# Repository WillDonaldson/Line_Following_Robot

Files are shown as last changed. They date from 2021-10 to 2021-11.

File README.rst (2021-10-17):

Line Following Robot
====================

An open source beginner-friendly tutorial on building a line following robot with Arduino. 

Tutorial
--------
Hardware build instructions and software documentation here:

https://line-following-robot.willdonaldson.io/

Purchase
--------

This project is open source and a bill of materials is freely provided in the tutorial link (above). However, if you prefer to purchase a prepared robot kit that will also financially support the development of more open source projects then you can purchase the robot here:

<insert link>

License
-------
This project is licensed under the terms of the MIT license

Media
-----

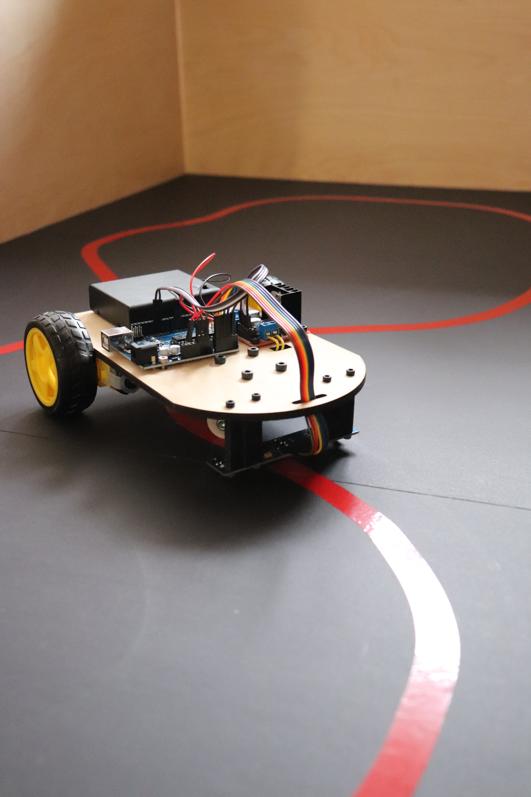
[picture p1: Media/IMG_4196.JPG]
Portrait of line following robot


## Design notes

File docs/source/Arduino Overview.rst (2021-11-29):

Arduino Overview
================

.. note::

   This project is under active development. More updates coming soon.

When documentation is complete this page will serve as a beginner friendly intro into programming with Arduino. In the meantime please refer to the `official Arduino resources <https://www.arduino.cc/reference/en/>`__.

Physical Board
--------------

Programming
-----------

Blink
-----

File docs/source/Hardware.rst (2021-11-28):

Hardware
========

This project is open source and a bill of materials is freely provided (below). However, if you prefer to purchase a prepared robot kit that will also financially support the development of more open source projects then you can purchase the robot here: <coming soon - insert link>

Bill of Materials
-----------------

**Off the shelf components**

* 1x Arduino Uno (with cable)
* 1x L298N Motor Driver
* 1x AA battery holder with ON/OFF switch (4 slots) 
* 4x AA batteries
* 2x Set of TT DC motor gearbox, wheel, mounting bracket, two M3 10mm bolts, two M3 30mm bolts, and two M3 nuts (usually sold all together)
* 1x One inch caster wheel
* 1x Five channel TCRT5000L array 
* 13x Male-Female jumper cables
* 2x Male-Male jumper cables
* 15x M3 12mm bolts
* 4x M4 20mm bolts
* 7x M3 nuts (optional use lock-nuts or loctite)
* 4x M4 nutes (optional use lock-nuts or loctite))
* Extra wire for motor leads (18 AWG - 22AWG)
* Zipties (optional for cable management)
* Double sided tape or hot glue for securing the battery pack

**Components to be fabricated**
See the next section for more details

* 1x Robot body (laser cut from 3mm to 5mm wood or acrylic)
* 1x Caster wheel spacer (3D printed)
* 2x Infrared sensor standoffs (3D printed)

**Tools**

* Soldering iron and solder
* Computer and approatiate dongle/cable for connecting to Arduino Uno
* Wire strippers (optional)
* Multimeter (optional - for diagnostics)

Manufacturing
-------------

When it comes to robotics, being able to fabricate custom components is extremely valuable, however buying your own 3D printer, laser cutter, and/or CNC machine is cost probihitive to starting a journey into robotics. Fortunately these custom pieces are available for purchase from my website <insert link - coming soon>. Alternatively online 3D printing services are available, and for some, these tools may be available locally at makerspaces, public libraries, or universities at little or no cost. These components are not dimension critical so they can also be fabricated by hand out of scrap wood and a hand drill or even out of sheets of cardboard.

**Robot body**

The SVG file for laser cutting the body can be downloaded `here <https://github.com/WillDonaldson/Line_Following_Robot/blob/main/Fabrication_Files/line-following-robot-frame.svg>`__. Birch wood is a great option as it is cheap and also compresses a little bit when the bolts are tightened, tereby preventing the bolts from vibrating loose. If using acrylic, it is recommended that you use lock-nuts or apply loctite to the bolts. If you do not have access to a laser cutter, you can print out the SVG file and use it as reference to cut your own robot frame out of cardboard or wood. 

**Caster wheel spacer**

File for 3D printing available `here <https://github.com/WillDonaldson/Line_Following_Robot/blob/main/Fabrication_Files/Wheel%20Spacer.3mf>`__.

**Infrared sensor standoffs**

File for 3D printing available `here <https://github.com/WillDonaldson/Line_Following_Robot/blob/main/Fabrication_Files/Infrared%20Sensor%20Standoff%20Bracket.3mf>`__.

Assembly
--------

**Step 1**
Mount the Arduino and motor driver in the orienation shown below using seven of the M3 12mm bolts and nuts

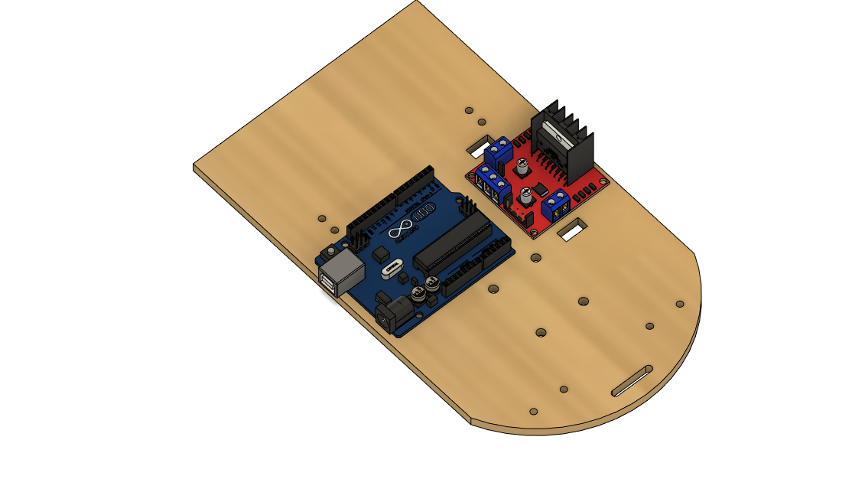
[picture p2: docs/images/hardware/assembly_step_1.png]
How to mount Arduino and motor driver


**Step 2**
Mount the motors to their brackets. Note the orienation of the motor pin orientation relative to the bracket. The image below shows the assembly for the right motor (left motor is the mirror image). Before mounting to the robot frame, solder wires to the motors to conect to the motor driver (length ~14cm).

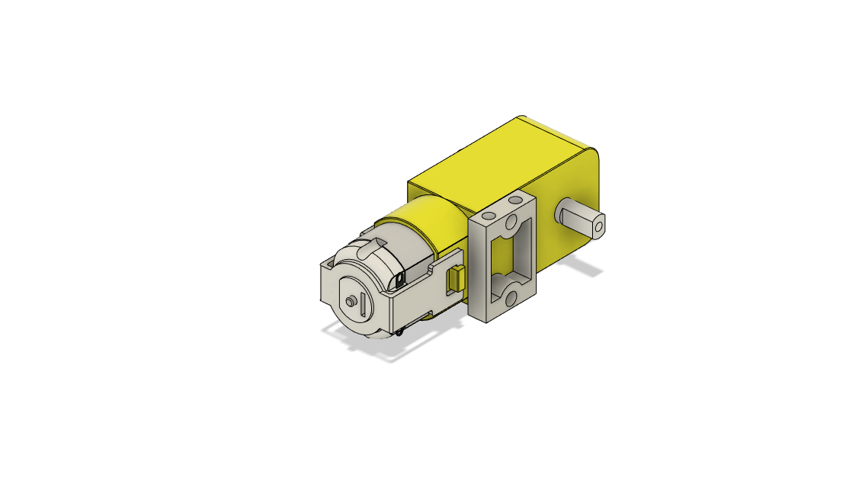
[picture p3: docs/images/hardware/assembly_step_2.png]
How to install the mount the motors to the mounting brackets


**Step 3**
Attach the motors using M3 bolts and the caster wheel using M4 bolts. Note the 3D printed caster wheel spacer.

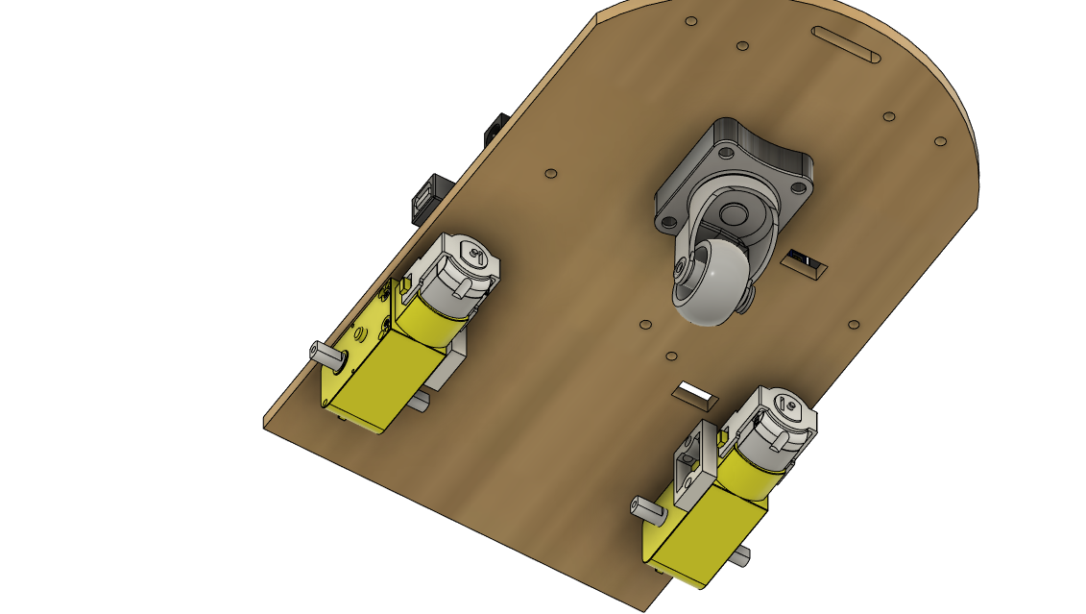
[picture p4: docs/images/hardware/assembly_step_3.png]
Install wheels on the robot frame


**Step 4**
Install the infrared sensor array using the 3D printed standoffs. Note the orientation of the header pins, they should face towards the front of the robot, if not they will collide with the caster wheel and make wiring more difficult.

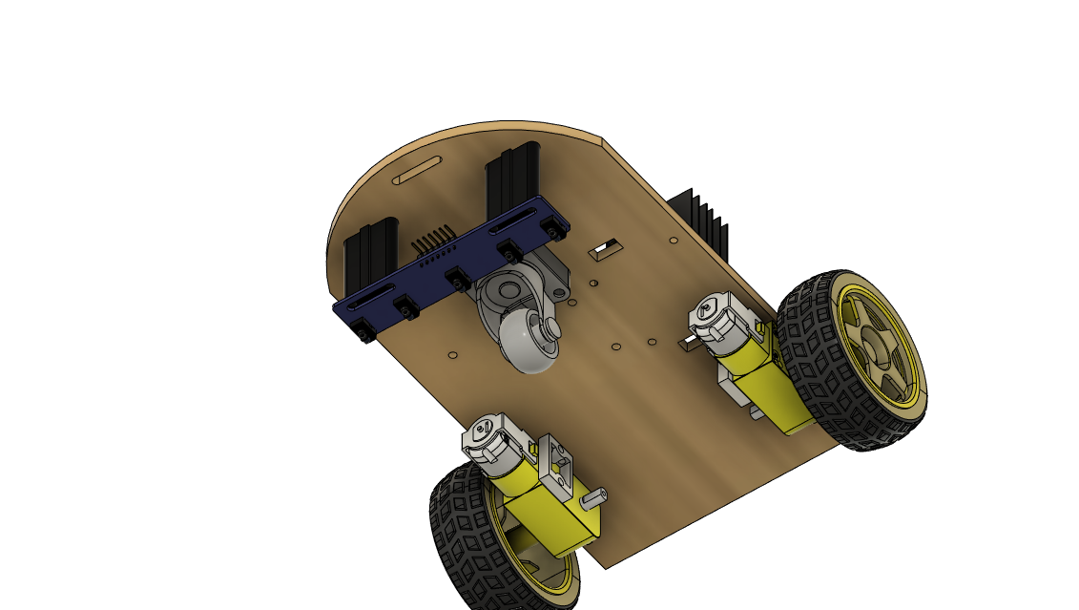
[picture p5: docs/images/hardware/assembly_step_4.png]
Install the infrared sensor array using the 3D printed standoffs.


**Step 5**
Attach the battery pack using double sided tap or hot glue to secure in place.

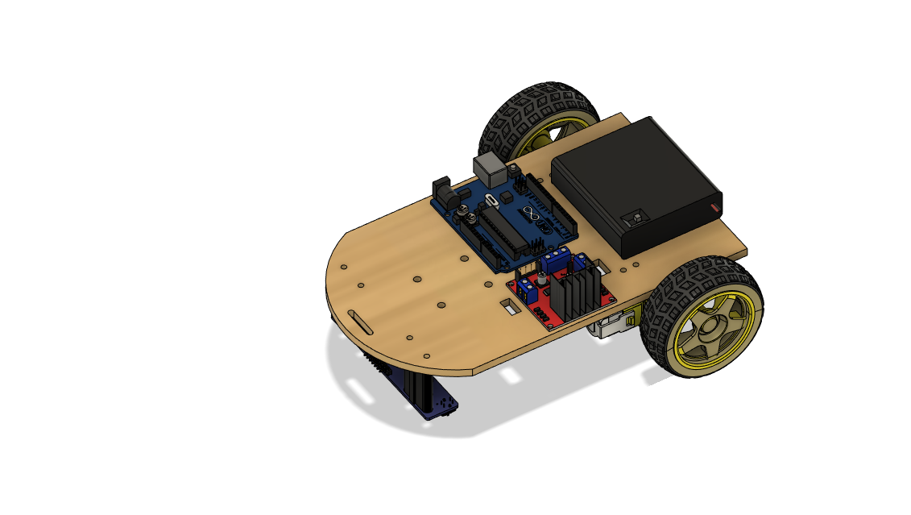
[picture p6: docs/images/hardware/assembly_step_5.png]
Attach the battery pack to robot


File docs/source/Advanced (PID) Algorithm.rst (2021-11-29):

Advanced (PID) Algorithm
========================

.. note::

   This project is under active development. More updates coming soon.

When documentation is complete this page will provide detailed steps and explanation of the code. In the meantime the source code is available for reference `here <https://github.com/WillDonaldson/Line_Following_Robot/tree/main/Arduino_Scripts>`__.

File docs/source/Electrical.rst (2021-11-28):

Electrical
==========

Overview
--------

Below the overall wiring schematic is shown. Scroll further down for a step by step breakdown. 

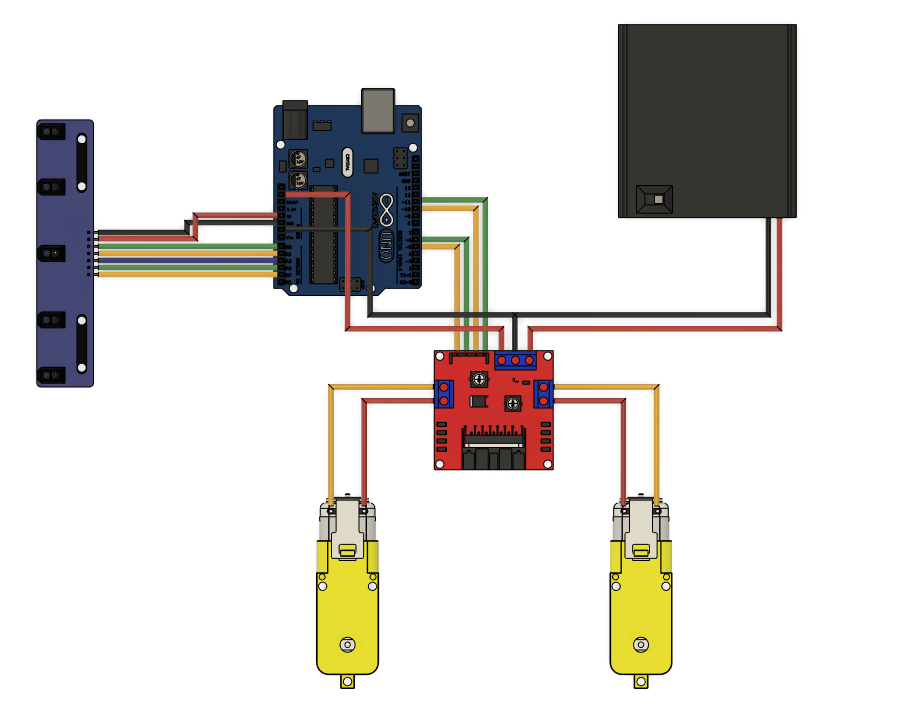
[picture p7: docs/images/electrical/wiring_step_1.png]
Overview of the complete wiring diagram


Infrared Sensor
---------------

In the previous :ref:`hardware assembly section <Assembly>`, the infrared sensor was attached with the header pins facing towards the front of the robot. Confirm this is correct before proceeding. Using seven male-female header pins connect the infrared sensor to the arduino anaolg pins and power pins as shown below, note that there is a slot in the robots frame to pass the wires through. Ensure the power cables (GND and 5V) are crossed over as shown in the picture below.

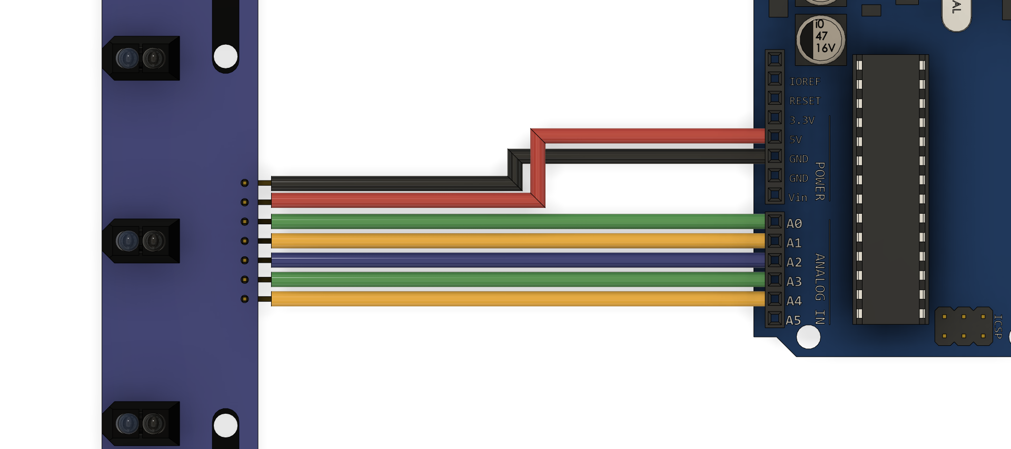
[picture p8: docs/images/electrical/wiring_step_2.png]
Electrical connections to the infrared sensor array.


Motors 
------

Connect the motors the the L298N motor driver screw terminals using the wires that were soldered to the TT motor gearbox in the :ref:`hardware assembly section <Assembly>`. Use 4 male-female jumper cables to conenct the L298N motor driver to Arduino digital pins 5, 6, 10, and 11. Finally, confirm the three `header pin jumpers <https://www.sparkfun.com/products/9044>`__ are installed on the ENA, ENB, and 5V EN pins (as comes stock). More information on the L298N motor driver and header pins available `here <https://lastminuteengineers.com/l298n-dc-stepper-driver-arduino-tutorial/>`__.

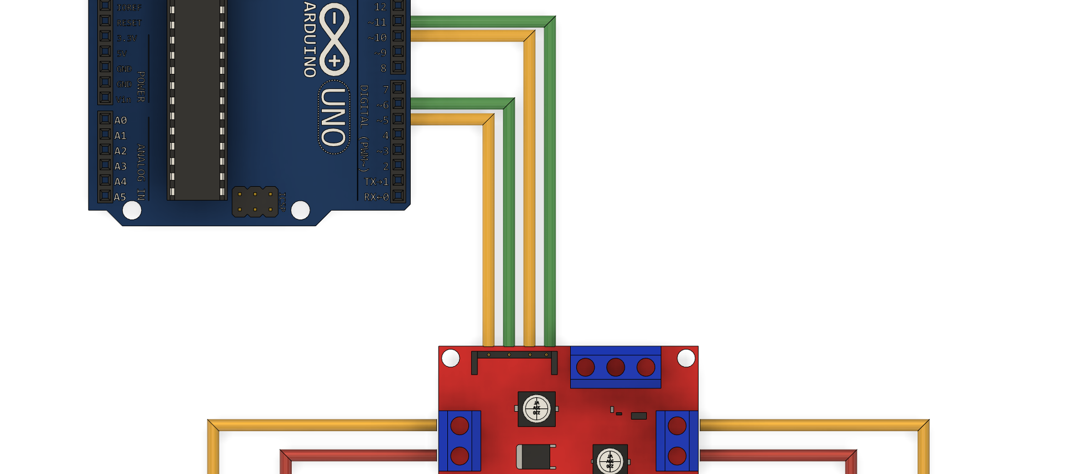
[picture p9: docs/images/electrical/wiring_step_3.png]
Connections between the motors and L298N motor drivers


Power
-----

To power the robot we will use 4 AA batteries in series giving a voltage of 6V. Make the connections below, note that the black ground wire from the battery is spliced (and ideally soldered) to a second black wire that connects to the GND pin of the Arduino. The red wire coming out of the L298N 5V terminal will power the Arduino. However we already occupied the 5V pin in the :ref:`infrared sensor electrical connection <Infrared Sensor>`. Thus instead we will connect this red 5V wire to the IOREF pin, which it the input/output reference voltage pin that connects to the Arduino logic voltage which just so happens to be 5V. 

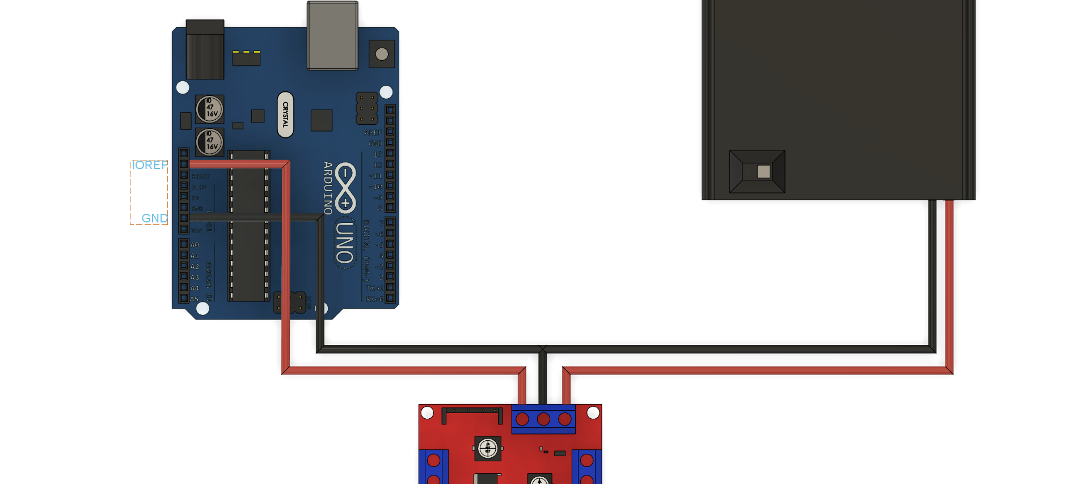
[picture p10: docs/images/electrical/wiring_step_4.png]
Connections to provide power to the robot


.. note::
   The L298N motor driver is incredibly inefficient (hence the large metal hink sink) and drops about 2V, meaning the motors are only getting around 4V. This is okay since the TT motors are rated for 3V - 6V, but if you want more power you could use a battery with a higher voltage such as a 7.4V lipo. While the L298N motor driver is inefficient it was chosen for this project as it is cheap, widely available, and there are plently of great online tutorials for beginners. I would recommend using this motor driver for most beginner projects and then switching to something like the slighty more expensive Cytron MDD10A motor driver down the line.

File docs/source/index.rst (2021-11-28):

Documentation for building a line following robot!
=================================================================

This project aims to provide step by step instruction to building your first robot from scratch. This beginner friendly project has no prerequistes but will link to additional external resources for gaining a deeper understanding and taking your new skills to the next level.

The robot uses a two motor differential drive with a freely spinning caster wheel at the front of the robot. The array of infrared sensors detect reflected light to deterimine if the sensor is over a dark material (no reflection) or light material (reflection). 

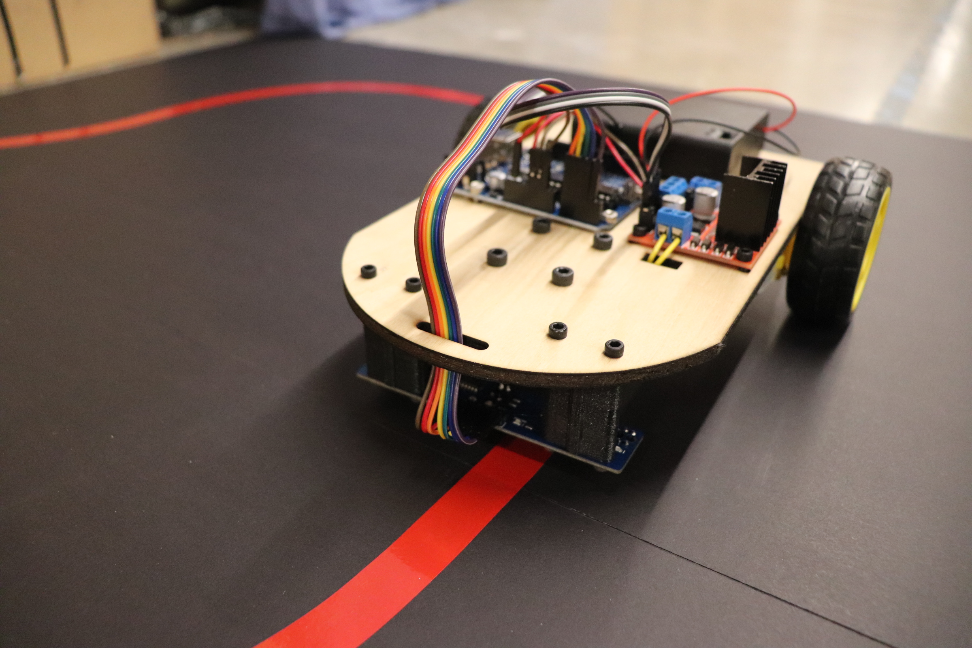
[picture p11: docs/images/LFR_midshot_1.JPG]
Image of assembled line following robot


.. note::

   This project is under active development. More updates coming soon.

Contents
--------

.. toctree::

   Hardware
   Electrical
   Arduino Overview
   Sensors and Actuators
   Bang-Bang Algorithm
   Advanced (PID) Algorithm
   Debugging, Troubleshooting, and Resources
   Related Projects

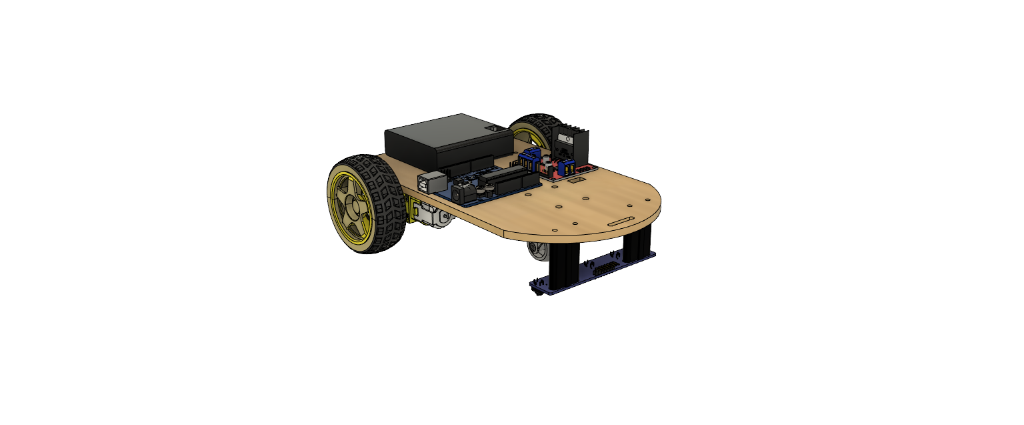
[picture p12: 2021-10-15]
Media/Line Following Robot CAD model pic3.png

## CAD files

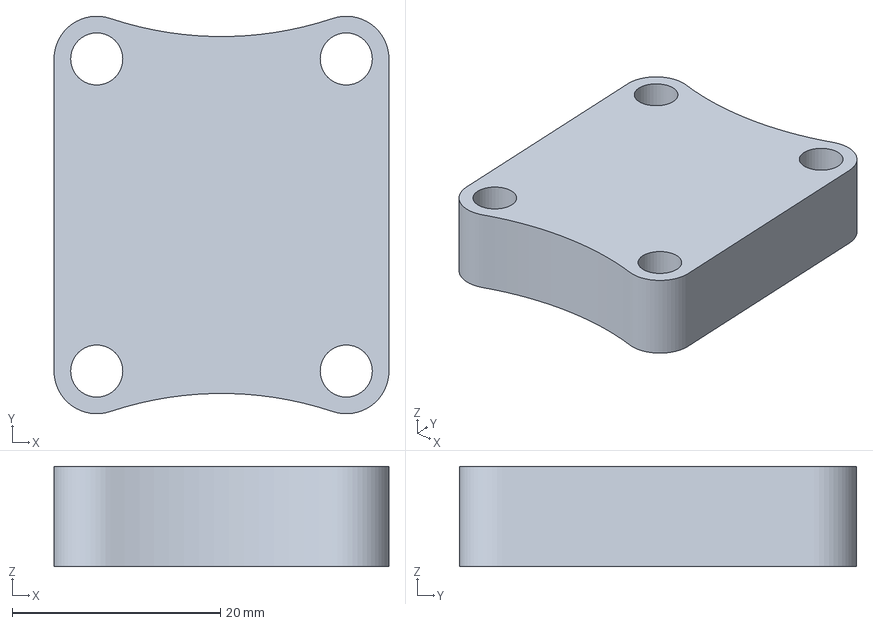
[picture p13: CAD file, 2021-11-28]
Fabrication_Files/Wheel Spacer.3mf
32.2 x 38.1 x 9.60 mm

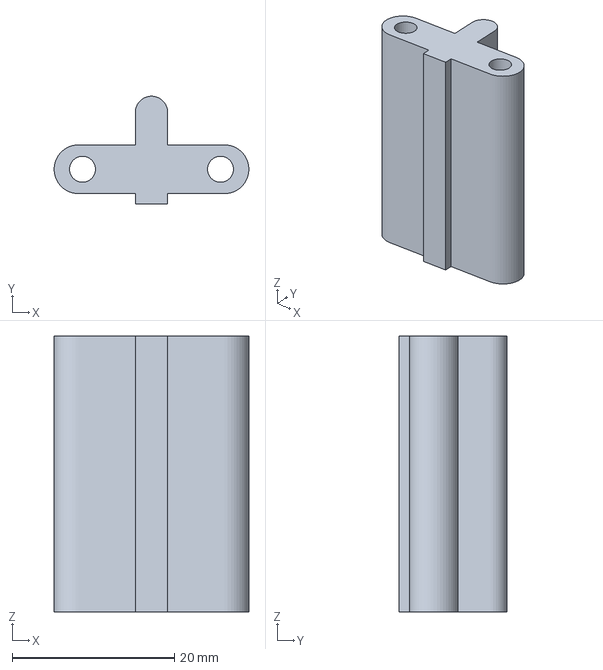
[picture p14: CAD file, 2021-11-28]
Fabrication_Files/Infrared Sensor Standoff Bracket.3mf
24.0 x 13.2 x 34.0 mm

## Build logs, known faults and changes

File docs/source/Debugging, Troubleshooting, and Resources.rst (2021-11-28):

Debugging, Troubleshooting, and Resources
=========================================

.. note::

   This project is under active development. More updates coming soon.

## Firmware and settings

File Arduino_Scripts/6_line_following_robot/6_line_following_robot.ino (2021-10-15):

#define motor1A 11 
#define motor1B 10 
#define motor2A 6 
#define motor2B 5 

#define IRright A1
#define IRleft A3
int IRright_val = 0;
int IRleft_val = 0;

int Speed = 150;            // choose speed variable in range [0, 255]

int turn_subtract = 25;     // experiment with different values here
int turn_add = 25;

void setup(){
  Serial.begin(9600);
  pinMode(motor1A, OUTPUT);
  pinMode(motor1B, OUTPUT);
  pinMode(motor2A, OUTPUT);
  pinMode(motor2B, OUTPUT);
  pinMode(IRright, INPUT);
  pinMode(IRleft, INPUT);
}

void loop(){
  IRright_val = digitalRead(IRright);
  IRleft_val = digitalRead(IRleft);

  if(IRright_val == HIGH and IRleft_val == HIGH){
    // both sensors over white
    driveForward(Speed);
  }
  if(IRright_val == HIGH and IRleft_val == LOW){
    // left sensor over black
    turnLeft(Speed);
  }
  if(IRright_val == LOW and IRleft_val == HIGH){
    // right sensor over black
    turnRight(Speed);
  }
  if(IRright_val == LOW and IRleft_val == LOW){
    // both sensors over black
    driveStop();
  }
}

void driveForward(int Spd){
  analogWrite(motor1A, Spd);   
  analogWrite(motor1B, LOW);
  analogWrite(motor2A, Spd);
  analogWrite(motor2B, LOW);
}

void driveBackward(int Spd){
  analogWrite(motor1A, LOW);   
  analogWrite(motor1B, Spd);
  analogWrite(motor2A, LOW);
  analogWrite(motor2B, Spd);
}

void driveStop(){
  analogWrite(motor1A, LOW);
  analogWrite(motor1B, LOW);
  analogWrite(motor2A, LOW);
  analogWrite(motor2B, LOW);
}

void turnRight(int Spd){
  analogWrite(motor1A, Spd+turn_add);
  analogWrite(motor1B, LOW);
  analogWrite(motor2A, LOW);
  analogWrite(motor2B, Spd-turn_subtract);
}

void turnLeft(int Spd){
  analogWrite(motor1A, LOW);
  analogWrite(motor1B, Spd-turn_subtract);
  analogWrite(motor2A, Spd+turn_add);
  analogWrite(motor2B, LOW);
}

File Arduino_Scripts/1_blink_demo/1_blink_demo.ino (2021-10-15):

#define LED_pin 13                  // assign pin LED is connected to

void setup(){                       // setup() is a block of code that runs once at the start of the program
  pinMode(LED_pin, OUTPUT);         // set pin to the output mode
}

void loop(){                        // loop() is a block of code that repeats itself until power is turned off
  digitalWrite(LED_pin, HIGH);      // turn LED on
  delay(100);                       // delay for 0.1 seconds while the LED is ON
  digitalWrite(LED_pin, LOW);       // turn LED off
  delay(100);                       // delay for 0.1 seconds while the LED is OFF
}

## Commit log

2021-11-28 addition of files to be fabricated
    [Infrared Sensor Standoff Bracket.3mf, Wheel Spacer.3mf]
2021-11-28 creation of electrical/wiring documentation
